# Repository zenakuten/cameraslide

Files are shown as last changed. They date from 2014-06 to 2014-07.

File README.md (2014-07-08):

#Camera slider

camera slider

Camera slider used for focus stacking and time lapse photography.  It interprets g-code and
accepts an M240 command to take a photograph remotely using an infrared LED.  The remote control 
is compatible with most Canon cameras.

#Usage

Once constructed, use a terminal program with XON/XOFF flow control 
such as [putty](http://www.chiark.greenend.org.uk/~sgtatham/putty/download.html), 
and then upload or cut/paste the g-code commands to it. 

Arrange the infrared LED so that it has line-of-sight to the front of 
the camera where the sensor is located. In the camera controls, you'll need to enable
the timed/remote mode, and once enabled make sure it is in remote mode instead of timed mode.  

An example script might look like:

      g28
      g0 x10
      m240
      g4 p1
      g0 x10.5
      m240
      g4 p1
      g0 x11
      m240
      g4 p1
      g0 x11.5
      m240
      g4 p1
      g0 x12
      ...
      g28

This translates to:

      Home
      move to position 10mm
      take a picture
      pause 1 second 
      move to position 10.5mm
      take a picture
      pause 1 second 
      move to position 11mm
      take a picture
      ...etc.

#Source

Source is available [here](cameraslide.ino).  It is a modified version of 
Dan Royer's [GcodeCNCDemo](https://github.com/MarginallyClever/GcodeCNCDemo) (2 axis, V1). It was
modified to work with a polulu 8825 stepper driver, and added support for the camera IR signal,
endstop trigger support, and flow control support.

STL files are available [here](stl), and OpenSCAD files are [here](scad)

[More images on imgur](http://imgur.com/a/SMLx9#0)

[Video](http://www.youtube.com/watch?v=6ovWjnzBGUw)

TODO - Need to get images of the output! soon...

#Hardware

[1/4 in.-20 x 7/8 in coupling nut](http://www.homedepot.com/p/Everbilt-1-4-in-20-x-7-8-in-Zinc-Plated-Rod-Coupling-Nut-15-Pieces-19117/202249719 )

They have packs of 3 in the store.

[1/4 in x 72  in. Plain Steel Round Rod](http://www.homedepot.com/p/Everbilt-1-4-in-x-72-in-Plain-Steel-Round-Rod-49060/202183538)

I cut two pieces to length and then polished them by putting each in my drill and using [polishing compound.](http://www.homedepot.com/p/Ryobi-Hard-Metal-Cleaning-Compound-Set-A04HM01/202886264)

[1/4 in 12 in Stainless Steel Threaded Rod](http://www.homedepot.com/p/Crown-Bolt-1-4-in-x-12-in-Stainless-Steel-Threaded-Rod-43540/203122557)

Don't get the zinc plated stuff, search around for the stainless.

[608 skate bearings](http://www.amazon.com/VXB-Skateboard-Bearings-Double-Shielded/dp/B002BBGTK6)

I had left overs, but you only need two.  I believe Ace Hardware sells them as well, as will any skate shop.

This stuff is optional, but it's what I used as a base (also left overs)

[Aluminum angle](http://www.homedepot.com/p/Unbranded-1-in-x-96-in-Aluminum-Angle-Bar-with-1-20-in-Thick-802587/204273981)

[Aluminum extrusion](http://us.misumi-ec.com/vona2/mech/M1500000000/M1501000000/M1501010000/M1501010300/)

Since the extrusion is a little harder to come by I'd recommend simply building the base out of wood.  

The rest of the screws are either M3 in various sizes (m3x30,m3x20,m3x16?I do not remember all of them sorry), or the bigger M8 used 
to connect everything to the extrusion.

#Electronics

[Arduino Nano](http://arduino.cc/en/Main/ArduinoBoardNano)

[8825 stepper driver](http://www.pololu.com/product/2133)

[Infrared LED](http://www.radioshack.com/product/index.jsp?productId=2062565) (I bought this in a brick and mortar store)

[Cherry switch](http://na.suzohapp.com/all_catalogs/electrical_supplies/95-0733-90) (not exact, I had an old cherry video game switch)

[Power connector](http://www.digikey.com/product-detail/en/PJ-037A/CP-037A-ND/1644545)

You'll also want header pins and connectors to connect everything, all stuff I bought off digikey.  
I used a 12V, 1.5A wall wart power supply that I bought at Goodwill.  Anything 12V 1A+ will be good enough.

I do not have a schematic but the wiring is very straight forward.  Everything was soldered together using [perfboard prototyping](http://www.youtube.com/watch?v=3N3ApzmyjzE)

Arduino Pins (configurable in the software):

- 4 -> DRV8825 step
- 5 -> DRV8825 dir
- 8 -> Cherry switch (other end of switch goes to ground)
- 6 -> 180 ohm resistor in series with the LED.  The LED should be connected with long wires so 
       it can be placed in front of the camera where the remote control sensor is.

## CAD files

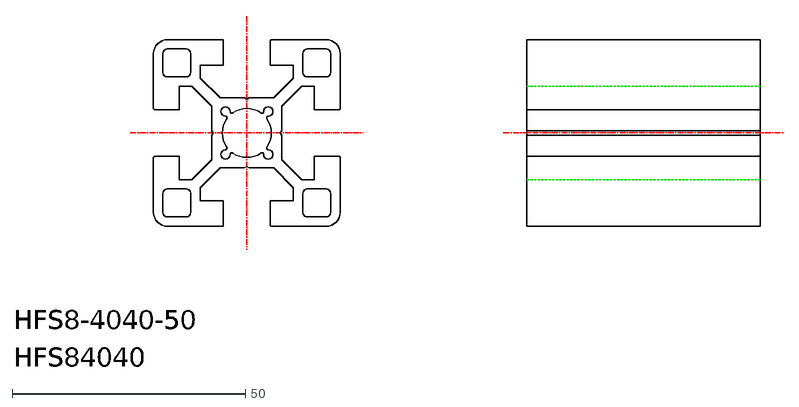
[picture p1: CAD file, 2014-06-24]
scad/hfs8-4040.dxf
HFS84040
HFS8-4040-50

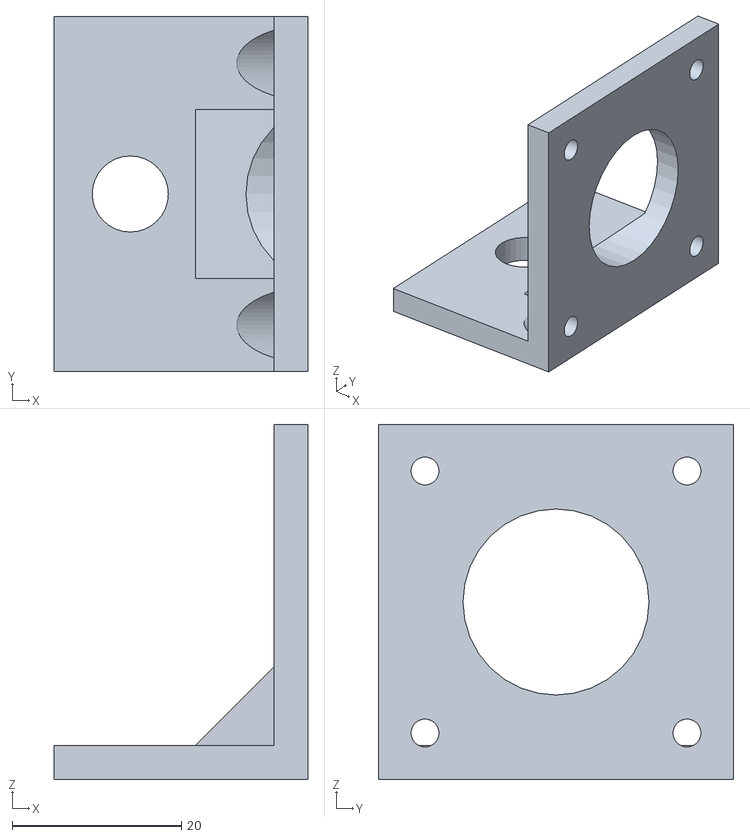
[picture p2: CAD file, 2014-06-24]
stl/motormounttop.stl
30.0 x 42.0 x 42.0

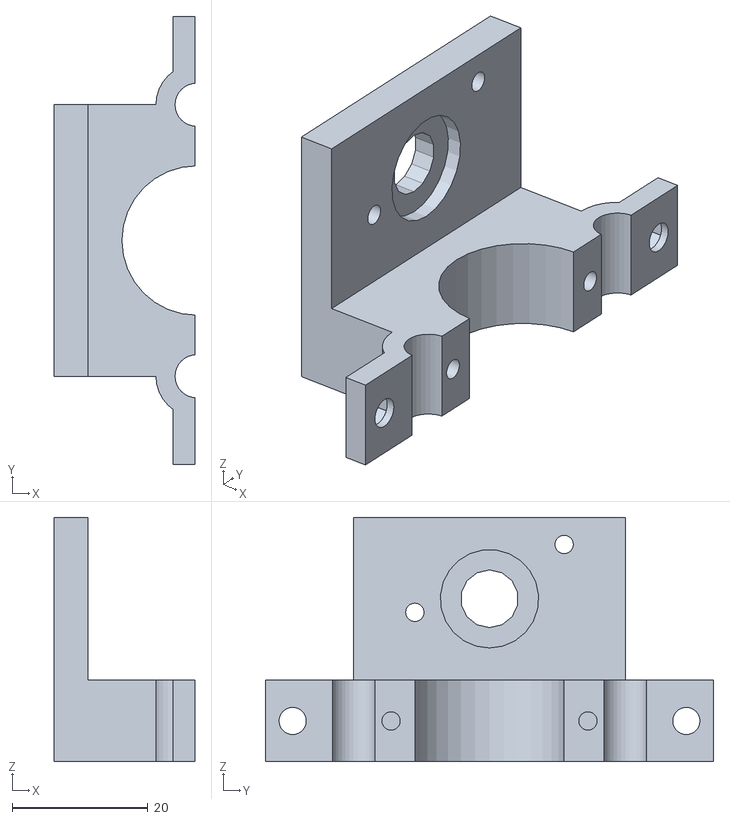
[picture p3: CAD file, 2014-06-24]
stl/sidemountbottom.stl
20.8 x 66.0 x 36.0

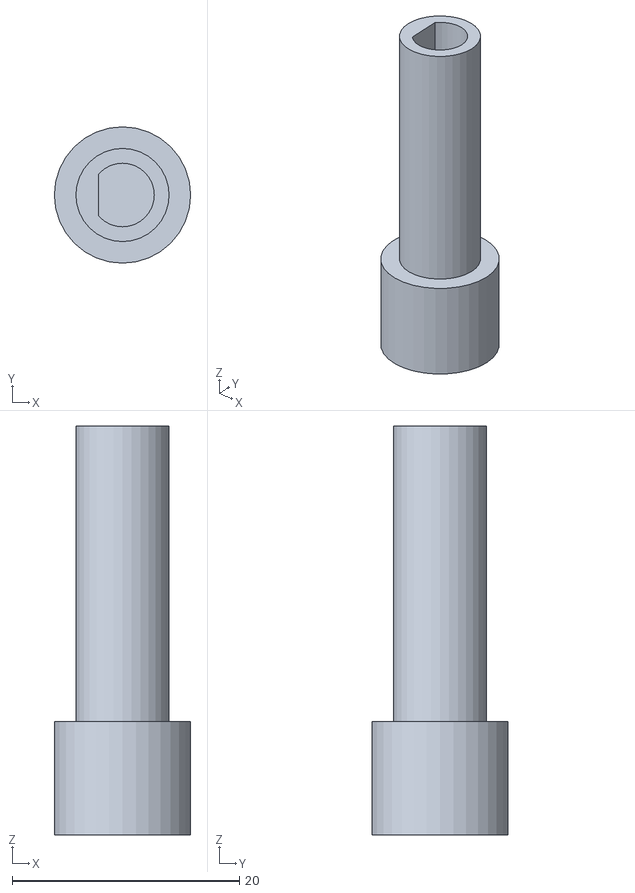
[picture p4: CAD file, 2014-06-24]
stl/motorcoupling.stl
12.0 x 12.0 x 36.0

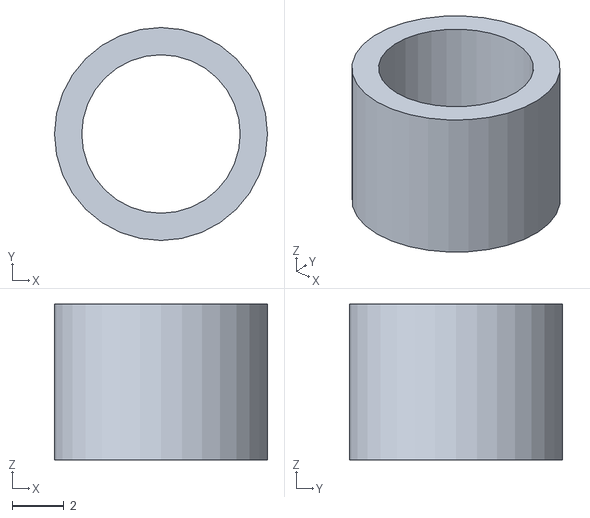
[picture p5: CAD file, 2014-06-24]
stl/shim.stl
8.20 x 8.20 x 6.00

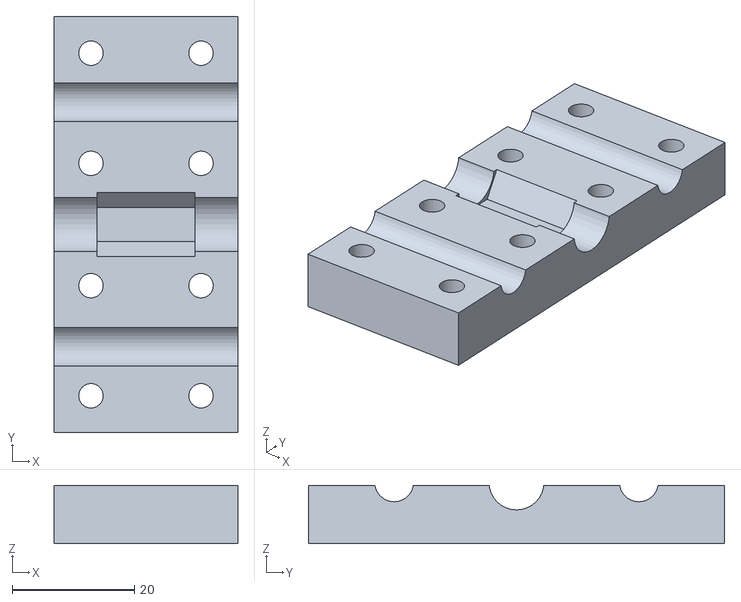
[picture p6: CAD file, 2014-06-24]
stl/centermountbottom.stl
30.0 x 68.0 x 9.50

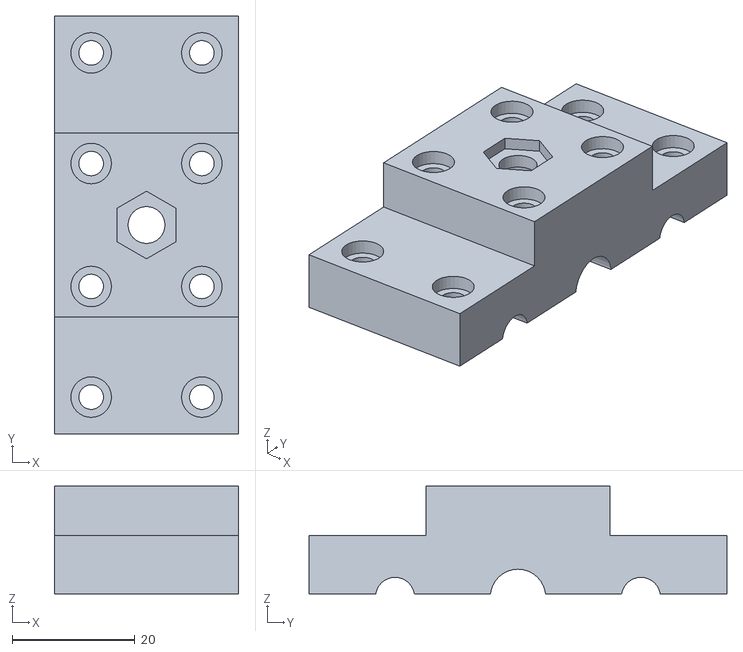
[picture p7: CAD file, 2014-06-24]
stl/centermounttop.stl
30.0 x 68.0 x 17.5

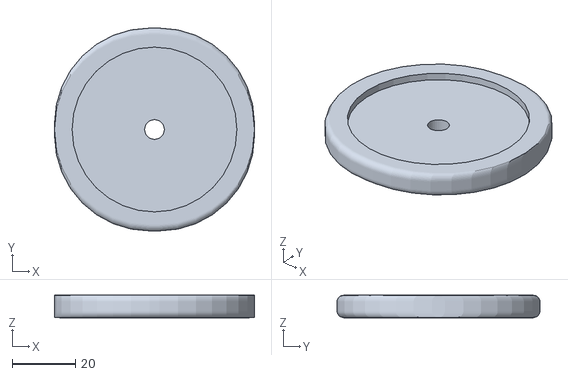
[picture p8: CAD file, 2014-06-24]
stl/knob.stl
63.1 x 64.0 x 7.10

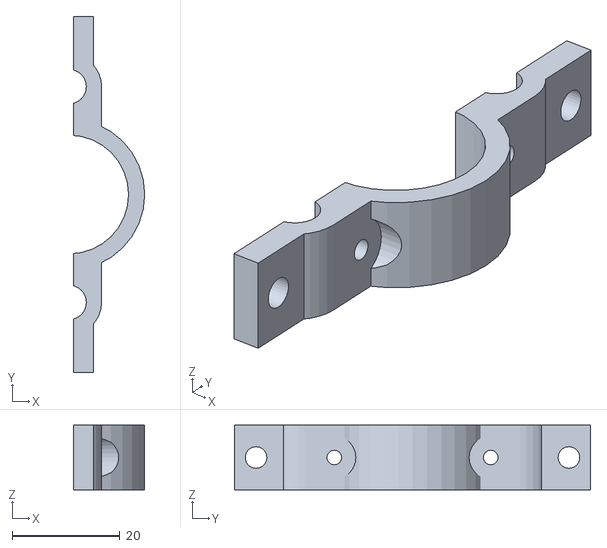
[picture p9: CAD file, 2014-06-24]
stl/sidemounttop.stl
13.2 x 66.0 x 12.0

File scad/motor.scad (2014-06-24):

include <nema.scad>

module motor()
{
	rotate([-90,0,0]) translate([0,40,0]) nema17(47);
}

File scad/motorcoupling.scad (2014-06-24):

module motorcoupling()
{
	difference()
	{
		union()
		{
			translate([0,0,-5]) cylinder(r=12/2,h=10,center=true,$fn=32);
			translate([0,0,12]) cylinder(r=8.2/2,h=28,center=true,$fn=32);
		}
		translate([0,0,-8 - 0.1]) cylinder(r=6.2/2,h=12,center=true,$fn=32);
		intersection()
		{
			translate([0,0,20 + 0.1]) cylinder(r=5.6/2,h=28,center=true,$fn=32);
			translate([2.9,0,20 + 0.1]) cube([10,10,28],center=true);
		}
	}
}

motorcoupling();

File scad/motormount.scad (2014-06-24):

include <motor.scad>

module motormount()
{
	difference()
	{
		union()
		{
			rotate([0,90,0])
			{
				cube([42,42,4], center=true);
				difference()
				{
					translate([19,0,-13]) cube([4,42,30], center=true);
					translate([15.5,15.5,0]) rotate([0,30,0]) cylinder(h=26,r=9/2,center=true);
					translate([15.5,-15.5,0]) rotate([0,30,0]) cylinder(h=26,r=9/2,center=true);
				}
			}

			intersection()
			{
				translate([-19,0,-13]) cube([42,42,16],center=true);
				translate([4,0,-13]) rotate([0,-45,0]) cube([42,20,16],center=true);
			}
		}

		rotate([0,90,0])
		{	
			cylinder(h=11,r=22/2 + 1,center=true,$fn=32);
			translate([15.5,15.5,0]) cylinder(h=5,r=4/2,center=true);
			translate([15.5,-15.5,0]) cylinder(h=5,r=4/2,center=true);
			translate([-15.5,15.5,0]) cylinder(h=5,r=4/2,center=true);
			translate([-15.5,-15.5,0]) cylinder(h=5,r=4/2,center=true);
		}
		translate([-19,0,-19]) cylinder(h=6,r=9/2 + 0.5,center=true,$fn=32);
	}
}

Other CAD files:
scad/motormounttop.scad
scad/cameramount.scad
scad/centermount.scad
scad/centermountbottom.scad
scad/centermountscrew.scad
scad/centermounttop.scad
scad/cherry.scad
scad/knob.scad
scad/nema.scad
scad/screwnut.scad
scad/shim.scad
scad/sidemount.scad
scad/sidemountbottom.scad
scad/sidemounttop.scad

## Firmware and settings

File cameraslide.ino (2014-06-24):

//------------------------------------------------------------------------------
// 2 Axis CNC Demo v1 - only supports motor shield v1
// dan@marginallycelver.com 2013-08-30
// zenakuten@yahoo.com 2014-06-11 - altered/branched for custom single axis system
//------------------------------------------------------------------------------
// Copyright at end of file.
// please see http://www.github.com/MarginallyClever/GcodeCNCDemo for more information.
//#define F_CPU 7900000 // clock frequency, set according to clock used!
#define F_CPU 16000000 // clock frequency, set according to clock used!

#include <inttypes.h>
#include <stdlib.h>
#include <avr/io.h>
#include <avr/sleep.h>
#include <util/delay.h>
#include <avr/interrupt.h>
//------------------------------------------------------------------------------
// CONSTANTS
//------------------------------------------------------------------------------
#define VERSION (1) // firmware version
#define BAUD (115200) // How fast is the Arduino talking?
#define MAX_BUF (64) // What is the longest message Arduino can store?
#define STEPS_PER_TURN (200) // depends on your stepper motor. most are 200.
#define STEPS_PER_MM (STEPS_PER_TURN/1.27) //steps per mm
#define MIN_STEP_DELAY (50.0)
#define MAX_FEEDRATE (1000000.0/MIN_STEP_DELAY)
#define MIN_FEEDRATE (0.01)


#define PIN_STEP (4)
#define PIN_DIR  (5)
#define PIN_ENDSTOP_X (8)
#define PIN_PHOTOGRAPH (6)

#define XOFF 19
#define XON  17


//------------------------------------------------------------------------------
// GLOBALS
//------------------------------------------------------------------------------
char buffer[MAX_BUF]; // where we store the message until we get a ';'
int sofar; // how much is in the buffer

float px=0.0, py=0.0; // location

// speeds
float fr=0; // human version
long step_delay; // machine version

// settings
char mode_abs=1; // absolute mode?


//------------------------------------------------------------------------------
// METHODS
//------------------------------------------------------------------------------


/**
* delay for the appropriate number of microseconds
* @input ms how many milliseconds to wait
*/
void pause(long ms) {
  delay(ms/1000);
  delayMicroseconds(ms%1000); // delayMicroseconds doesn't work for values > ~16k.
}


/**
* Set the feedrate (speed motors will move)
* @input nfr the new speed in steps/second
*/
void feedrate(float nfr) {
  if(fr==nfr) return; // same as last time? quit now.

  if(nfr>MAX_FEEDRATE || nfr<MIN_FEEDRATE) { // don't allow crazy feed rates
    Serial.print(F("New feedrate must be greater than "));
    Serial.print(MIN_FEEDRATE);
    Serial.print(F("steps/s and less than "));
    Serial.print(MAX_FEEDRATE);
    Serial.println(F("steps/s."));
    return;
  }
  step_delay = 1000000.0/nfr;
  fr=nfr;
}


/**
* Set the logical position
* @input npx new position x
* @input npy new position y
*/
void position(float npx,float npy) {
  // here is a good place to add sanity tests
  px=npx;
  py=npy;
}


/**
* Uses bresenham's line algorithm to move both motors
* @input newx the destination x position
* @input newy the destination y position
**/
void line(float newx,float newy) {
  long dx=newx-px;
  long dy=newy-py;
  int dirx=dx>0?1:-1;
  int diry=dy>0?-1:1; // because the motors are mounted in opposite directions
  dx=abs(dx);
  dy=abs(dy);

  long i;
  long over=0;

  if(dx>dy) {
    for(i=0;i<dx;++i) {      
      //m1.onestep(dirx);
      onestepx(dirx);
      over+=dy;
      if(over>=dx) {
        over-=dx;
        //m2.onestep(diry);
      }
      pause(step_delay);
    }
  } else {
    for(i=0;i<dy;++i) {
      //m2.onestep(diry);
      over+=dx;
      if(over>=dy) {
        over-=dy;
        //m1.onestep(dirx);
        onestepx(dirx);
      }
      pause(step_delay);
    }
  }

  px=newx;
  py=newy;
}

//step via drv8825
void onestepx(int dir)
{
    if(digitalRead(PIN_ENDSTOP_X) == LOW && dir <= 0) {
      Serial.println("Endstop X triggered");
      return;
    }
    digitalWrite(PIN_DIR, dir > 0 ? 1 : 0);
    delay(1);
    digitalWrite(PIN_STEP, 1);
    delay(1);
    digitalWrite(PIN_STEP, 0); 
    delay(1);
}

void home() 
{  
   while(digitalRead(PIN_ENDSTOP_X) != LOW) {
     onestepx(-1);
     pause(10);
   }  
   position(0,0);
}


void takepicture()
{
	const uint8_t count=12;
	for(int i=0; i < count; i++) {
		digitalWrite(PIN_PHOTOGRAPH, HIGH);
		delayMicroseconds(10);
		digitalWrite(PIN_PHOTOGRAPH, LOW);
		delayMicroseconds(10);
	}
	delayMicroseconds(7330);
	for(int i=0; i < count; i++) {
		digitalWrite(PIN_PHOTOGRAPH, HIGH);
		delayMicroseconds(10);
		digitalWrite(PIN_PHOTOGRAPH, LOW);
		delayMicroseconds(10);
	}
}

/**
* Look for character /code/ in the buffer and read the float that immediately follows it.
* @return the value found. If nothing is found, /val/ is returned.
* @input code the character to look for.
* @input val the return value if /code/ is not found.
**/
float parsenumber(char code,float val) {
  char *ptr=buffer;
  while(ptr && *ptr && ptr<buffer+sofar) {
    if(toupper(*ptr)==code) {
      return atof(ptr+1);
    }
    ptr=strchr(ptr,' ')+1;
  }
  return val;
}


/**
* write a string followed by a float to the serial line. Convenient for debugging.
* @input code the string.
* @input val the float.
*/
void output(char *code,float val) {
  Serial.print(code);
  Serial.println(val);
}


/**
* print the current position, feedrate, and absolute mode.
*/
void where() {
  output("X",px);
  output("Y",py);
  output("F",fr);
  Serial.println(mode_abs?"ABS":"REL");
}


/**
* display helpful information
*/
void help() {
  Serial.print(F("GcodeCNCDemo2AxisV1 "));
  Serial.println(VERSION);
  Serial.println(F("Commands:"));
  Serial.println(F("G00 [X(steps)] [Y(steps)] [F(feedrate)]; - linear move"));
  Serial.println(F("G01 [X(steps)] [Y(steps)] [F(feedrate)]; - linear move"));
  Serial.println(F("G04 P[seconds]; - delay"));
  Serial.println(F("G28; - home"));
  Serial.println(F("G90; - absolute mode"));
  Serial.println(F("G91; - relative mode"));
  Serial.println(F("G92 [X(steps)] [Y(steps)]; - change logical position"));
  Serial.println(F("M18; - disable motors"));
  Serial.println(F("M100; - this help message"));
  Serial.println(F("M114; - report position and feedrate"));
  Serial.println(F("M240; - Cannon DSLR remote picture"));
}


/**
* Read the input buffer and find any recognized commands. One G or M command per line.
*/
void processCommand() {
  int cmd = parsenumber('G',-1);
  switch(cmd) {
  case 0: // move linear
  case 1: // move linear
    feedrate(parsenumber('F',fr));
    line( (parsenumber('X',(mode_abs?px:0)) + (mode_abs?0:px))*STEPS_PER_MM,
          (parsenumber('Y',(mode_abs?py:0)) + (mode_abs?0:py))*STEPS_PER_MM );
    break;
  case 4: 
      delay(parsenumber('P', 0)*1000.0);
      break; // dwell
  case 28: home(); break;
  case 90: mode_abs=1; break; // absolute mode
  case 91: mode_abs=0; break; // relative mode
  case 92: // set logical position
    position( parsenumber('X',0),
              parsenumber('Y',0) );
    break;
  default: break;
  }

  cmd = parsenumber('M',-1);
  switch(cmd) {
    case 18: // disable motors
  //    m1.release();
  //    m2.release();
      break;
    case 100: help(); break;
    case 114: where(); break;
    case 240: takepicture(); break;
    case 241: 
              digitalWrite(PIN_PHOTOGRAPH, HIGH);  //led test
              delay(3000);
              digitalWrite(PIN_PHOTOGRAPH, LOW);
         break;
    default: break;
  }
}


/**
* prepares the input buffer to receive a new message and tells the serial connected device it is ready for more.
*/
void ready() {
  sofar=0; // clear input buffer
  Serial.print(F(">")); // signal ready to receive input
}


/**
* First thing this machine does on startup. Runs only once.
*/
void setup() {
  pinMode(PIN_DIR, OUTPUT);
  pinMode(PIN_STEP, OUTPUT);
  pinMode(PIN_PHOTOGRAPH, OUTPUT);
  pinMode(PIN_ENDSTOP_X, INPUT_PULLUP);
  
  Serial.begin(BAUD); // open coms
  help(); // say hello
  position(0,0); // set staring position
  feedrate((MAX_FEEDRATE + MIN_FEEDRATE)/2); // set default speed
  ready();
}


/**
* After setup() this machine will repeat loop() forever.
*/
void loop() {
  // listen for serial commands
  while(Serial.available() > 0) { // if something is available
    char c=Serial.read(); // get it
    Serial.print(c); // repeat it back so I know you got the message
    if(sofar<MAX_BUF) buffer[sofar++]=c; // store it
    if(buffer[sofar-1]==';' || buffer[sofar-1] == '\n' || buffer[sofar-1] == '\r') break; // entire message received
  }

  if(sofar>0 && (buffer[sofar-1]==';' || buffer[sofar-1]=='\n' || buffer[sofar-1] =='\r')) {
    // we got a message and it ends with a semicolon
    buffer[sofar]=0; // end the buffer so string functions work right
    Serial.print(F("\r\n")); // echo a return character for humans
    Serial.write(XOFF);
    processCommand(); // do something with the command
    ready();
    Serial.write(XON);
  }
}

/**
* This file is part of GcodeCNCDemo.
*
* GcodeCNCDemo is free software: you can redistribute it and/or modify
* it under the terms of the GNU General Public License as published by
* the Free Software Foundation, either version 3 of the License, or
* (at your option) any later version.
*
* GcodeCNCDemo is distributed in the hope that it will be useful,
* but WITHOUT ANY WARRANTY; without even the implied warranty of
* MERCHANTABILITY or FITNESS FOR A PARTICULAR PURPOSE. See the
* GNU General Public License for more details.
*
* You should have received a copy of the GNU General Public License
* along with Foobar. If not, see <http://www.gnu.org/licenses/>.
*/
